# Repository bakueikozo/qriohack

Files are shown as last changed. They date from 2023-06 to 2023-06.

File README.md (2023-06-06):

# qriohack
Qrio Lock 初代(Q-SL1)をハックするための知見と  
内蔵マイコンを書き換えるためのファームを生成するためのソースコードです

# 現状の実装
設定に追加のシリアルポートが必要
鍵を施錠位置に合わせて取り付けて'P'コマンドで初期位置入力  
続けて鍵を開錠位置に合わせて取り付けて'P'コマンドで第二位置入力すると記憶される  
開錠したいときはシリアルから'U' 、施錠は'L'を送る  
もしくは、BLE送信できる奴から特定のところに'U'か'L'を書き込むと動く  

これをアプリから送るようにUIを作ると今までのQrioのように作れます。
が、まだ作ってませんし、私が作るとは言ってません。
# どうやる
Windowsの場合
WICED-SDKをダウンロードしてきて、Apps以下にこのリポジトリ内のApps/obaqフォルダをコピーします
コマンドプロンプトから
> make obaq-BCM920737TAG_Q32

でビルドできるか確認

OKなら
> make obaq-BCM920737TAG_Q32 download UART=COMxx

で書き込み

WICED-SDKは
https://community.infineon.com/t5/Public-Archive/WICED-Smart-SDK-2-2-3-7z-Archive/td-p/247688

ここにある奴で確認済み
そのほかのバージョンやIDEにインポートするなら各自

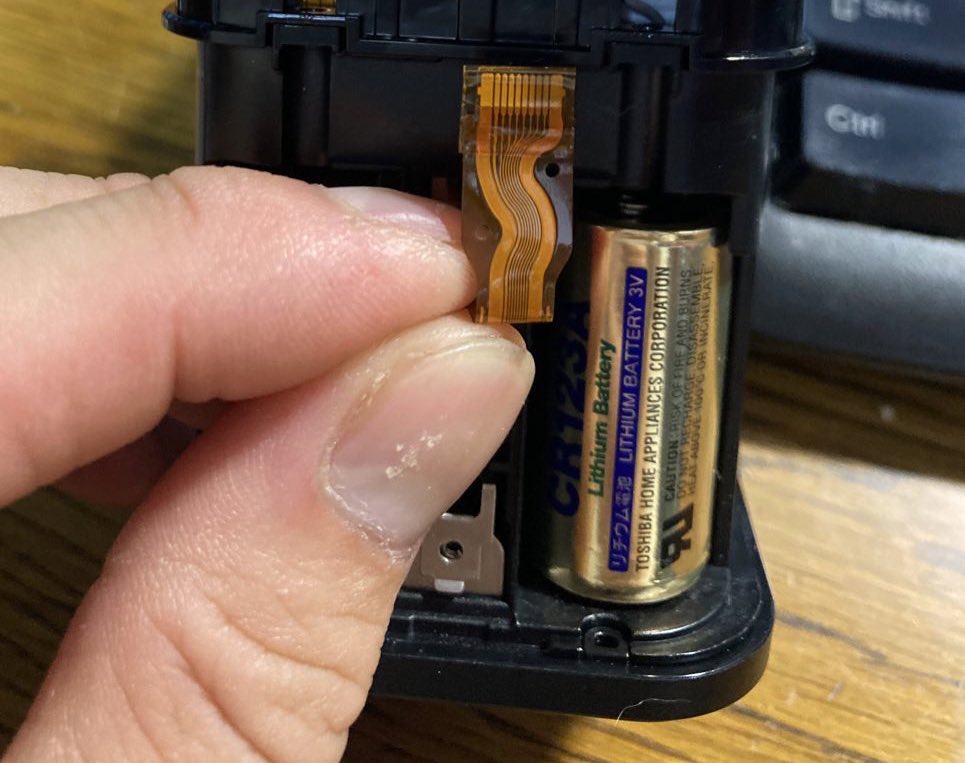
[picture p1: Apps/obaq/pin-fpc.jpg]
書き込みコネクタ


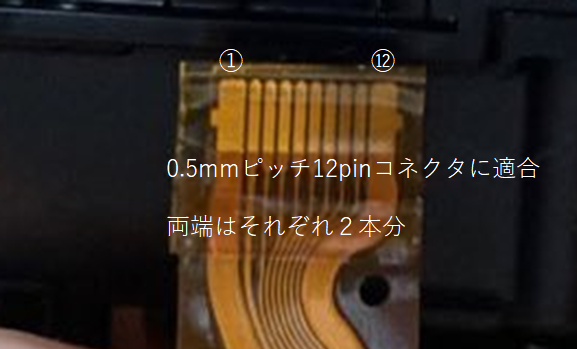
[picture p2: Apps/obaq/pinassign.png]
ピンアサイン ピン番号の見方


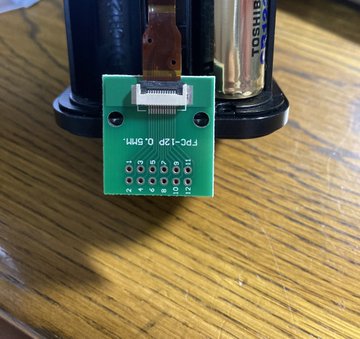
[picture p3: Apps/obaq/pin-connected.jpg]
変換基板に取り付けた場合


# ピンアサイン
下面接続のFPC基板に取り付けた場合、この説明の番号と一致します  
使ったやつはこれ　 https://amzn.to/43Kj0qI  
|  No. |  Function  |
| ---- | ---- |
|  1,2  |  6V  |
|  3  |  3.3V  |
| 4 | RESET(NC:基板上ジャンパ)  
| 5 |SCL(NC:基板上ジャンパ)  |
| 6 | SDA(NC:基板上ジャンパ) |
| 7 |peripheral UART TXD in  |
| 8 |peripheral UART RXD out  |
| 9 |Programming RXD  |
| 10 |Programing TXD  |
| 11,12 |GND  |

1,2および3　は基板上の電源パターン直結のため、電池が入っているときの挙動に注意  
4,5,6は基板まで届いているが、基板上でジャンパがNCになっているのでそのままでは使用不可   
9,10と3,11,12の接続で書き込み可能。電源投入時に9をHighにしておくとProgrammingモードに入る   

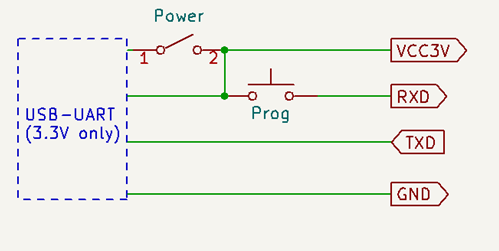
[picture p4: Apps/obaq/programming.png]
書き込み回路


追加のシリアルポートが欲しい場合は7,8を使う  

※参考※  
https://community.infineon.com/t5/Resource-Library/Programming-the-TAG2-TAG3-Board-using-command-line-tools/ta-p/246905  
書き込み中に電源を落としてしまった場合正常に起動しなくなる。その場合downloadではなくrecoveryモードに入る必要がある。  
電源投入orRESETの際にeepromのSDAをVCCに吊るとソフトが読み込めない→リカバリモードになる  
ここでrecoveryで書き込む

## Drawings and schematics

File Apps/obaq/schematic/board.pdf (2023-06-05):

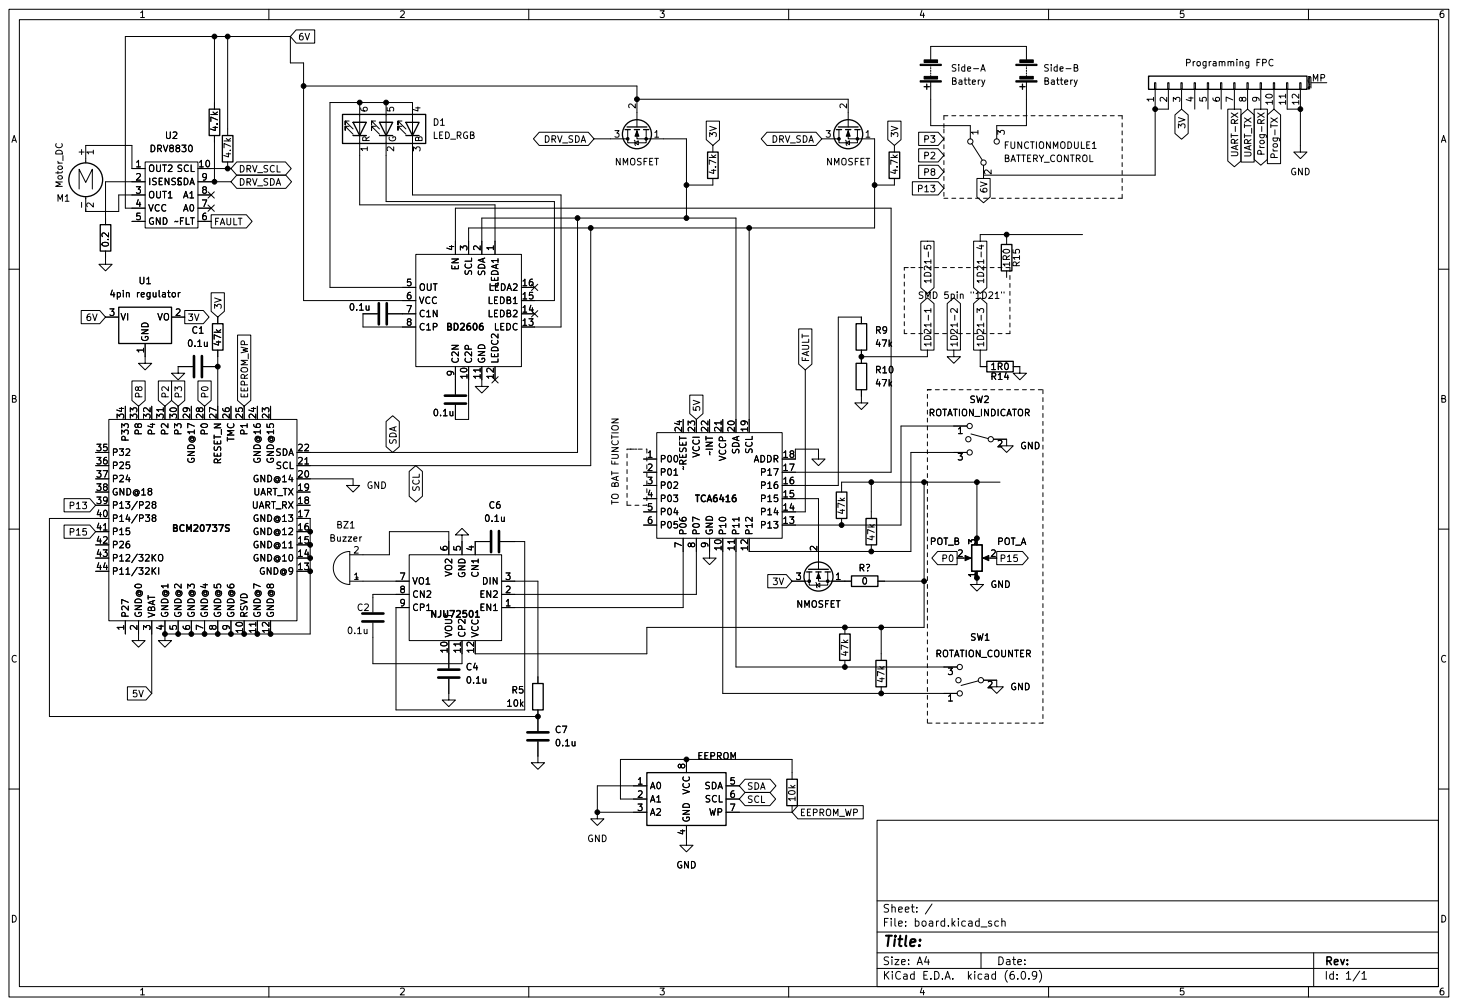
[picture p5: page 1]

2 GND@14 20 SCL 21 SDA 22 GND@15 23 GND@16 24 P1 25 TMC 26 RESET_N 27 P0 28 GND@17 29 VBAT

1 RSVD 10 GND@7 11 GND@8 12 GND@9 13 GND@10 14 GND@11 15 GND@12 16 GND@13 17 UART_RX 18 UART_TX 19 GND@0

4 SDA 5 SCL 6 WP 7 VCC

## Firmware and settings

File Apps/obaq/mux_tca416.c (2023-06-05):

// TCA6416A module
// Copyright 2019 Håkon Nessjøen
// https://github.com/haakonnessjoen/TCA6416A/


#include "bleprofile.h"
#include "bleapp.h"
#include "gpiodriver.h"
#include "string.h"
#include "stdio.h"
#include "platform.h"
#include "bleappconfig.h"
#include "cfa.h"


#include "mux_tca416.h"

void tca_begin(UINT8 address){
    ble_trace0("tca_begin\n");
	tca_i2caddr = 0x20 | address;
	tca_i2caddr =tca_i2caddr<<1 ;
	tca_i2cwidth = 2;

	tca_port_read();
	tca_mode_read();
    ble_trace0("tca_end\n");
}
void tca_pin_mode(UINT8 pinNum, int mode){
	UINT16 mask = 1 << pinNum;
    ble_trace0("tca_pin_mode\n");

	if (mode == TCA_PINMODE_INPUT) {
		tca_pinModes |= mask;
	} else {
		tca_pinModes &= ~mask;
	}

	tca_mode_write(tca_pinModes);
}


void tca_pin_write(UINT8 pinNum, UINT8 level){
	UINT16 mask = 1 << pinNum;
    ble_trace0("tca_pin_write\n");

	if (level == TCA_OUTPUT_HIGH) {
		tca_pinState |= mask;
	} else {
		tca_pinState &= ~mask;
	}

	tca_port_write(tca_pinState);
}
INT16  tca_pin_read(UINT8 pinNum){
	UINT16 mask = 1 << pinNum;
    ble_trace0("tca_pin_read\n");

	tca_port_read();

	if ((tca_pinState & mask) == mask) {
		return 1;
	} else {
		return 0;
	}
}
void tca_port_write(UINT16 i2cportval){

    CFA_BSC_STATUS read_status;
    UINT8 return_value = 0;

    UINT8 reg_bytes_to_write[3];
    reg_bytes_to_write[0] = TCAREG_OUTPUT0;
    reg_bytes_to_write[1] = i2cportval & 0xFF;
    reg_bytes_to_write[2] = (i2cportval >> 8) & 0xFF;
    ble_trace0("tca_port_write\n");

    // Invoke the lower level driver. Non-combo transaction, so set offset parameters to NULL/0.
    read_status = cfa_bsc_OpExtended(reg_bytes_to_write, sizeof(reg_bytes_to_write), NULL, 0, tca_i2caddr,
                                                I2C_SLAVE_OPERATION_WRITE);

    switch(read_status)
    {
        case CFA_BSC_STATUS_INCOMPLETE:
            // Transaction did not go through. ERROR. Handle this case.
            break;
        case CFA_BSC_STATUS_SUCCESS:
		    ble_trace0("i2c_write success\n");
            return_value = 1;
            break;
        case CFA_BSC_STATUS_NO_ACK:
            // No slave device with this address exists on the I2C bus. ERROR. Handle this.
        default:
            break;
    }

	tca_pinState = i2cportval;
}
UINT16 tca_port_read(){
// (UINT8 slave_address,UINT8 register_address, INT16* data// 

    CFA_BSC_STATUS read_status;
    UINT8 return_value = 0;

    UINT8 reg_read_bytes_to_write[1];
    UINT8 reg_bytes_to_read[2];
	INT16 data;
    ble_trace0("tca_port_read\n");
    
    reg_read_bytes_to_write[0] = TCAREG_INPUT0;

    // Do a combo write then read operation
    read_status = cfa_bsc_OpExtended(reg_bytes_to_read, sizeof(reg_bytes_to_read), reg_read_bytes_to_write,
                                                        sizeof(reg_read_bytes_to_write), tca_i2caddr,
                                                        I2C_SLAVE_OPERATION_READ);
    switch(read_status)
    {
        case CFA_BSC_STATUS_INCOMPLETE:
            // Transaction did not go through. ERROR. Handle this case.
            break;
        case CFA_BSC_STATUS_SUCCESS:
            // The read was successful.
            data = (INT16)(reg_bytes_to_read[0] | reg_bytes_to_read[1] << 8);
			tca_pinState = (tca_pinState & ~tca_pinModes) | (data & tca_pinModes);

		    ble_trace0("i2c_read success\n");

            return tca_pinState;
        case CFA_BSC_STATUS_NO_ACK:
            // No slave device with this address exists on the I2C bus. ERROR. Handle this.
        default:
            break;
    }

    return -1;

}
void tca_mode_write(UINT16 modes){
    CFA_BSC_STATUS read_status;
    UINT8 return_value = 0;

    UINT8 reg_bytes_to_write[3];
    ble_trace0("tca_mode_write\n");

    reg_bytes_to_write[0] = TCAREG_CONFIG0;
    reg_bytes_to_write[1] = modes & 0xFF;
    reg_bytes_to_write[2] = (modes >> 8) & 0xFF;

    // Invoke the lower level driver. Non-combo transaction, so set offset parameters to NULL/0.
    read_status = cfa_bsc_OpExtended(reg_bytes_to_write, sizeof(reg_bytes_to_write), NULL, 0, tca_i2caddr,
                                                I2C_SLAVE_OPERATION_WRITE);

    switch(read_status)
    {
        case CFA_BSC_STATUS_INCOMPLETE:
            // Transaction did not go through. ERROR. Handle this case.
		    ble_trace0("i2c_write INCOMP\n");
            break;
        case CFA_BSC_STATUS_SUCCESS:
            // The read was successful.
		    ble_trace0("i2c_write success\n");
            return_value = 1;
            break;
        case CFA_BSC_STATUS_NO_ACK:
		    ble_trace0("i2c_write NO_ACK\n");
            // No slave device with this address exists on the I2C bus. ERROR. Handle this.
        default:
		    ble_trace0("default\n");
            break;
    }


	tca_pinModes = modes;
}
UINT16 tca_mode_read(){
    CFA_BSC_STATUS read_status;
    UINT8 return_value = 0;

    UINT8 reg_read_bytes_to_write[1];
    UINT8 reg_bytes_to_read[2];
    ble_trace0("tca_mode_read\n");

    reg_read_bytes_to_write[0] = TCAREG_CONFIG0;

    // Do a combo write then read operation
    read_status = cfa_bsc_OpExtended(reg_bytes_to_read, sizeof(reg_bytes_to_read), reg_read_bytes_to_write,
                                                        sizeof(reg_read_bytes_to_write), tca_i2caddr,
                                                        I2C_SLAVE_OPERATION_READ);
    switch(read_status)
    {
        case CFA_BSC_STATUS_INCOMPLETE:
            // Transaction did not go through. ERROR. Handle this case.
            break;
        case CFA_BSC_STATUS_SUCCESS:
            // The read was successful.
            {
            INT16 data = (INT16)(reg_bytes_to_read[0] | reg_bytes_to_read[1] << 8);
            return_value = 1;

			/*
			tca_pinModes = TW.read();
			tca_pinModes |= TW.read() << 8;*/

			tca_pinModes = data;
		    ble_trace0("i2c_read success\n");
			}		
            break;
        case CFA_BSC_STATUS_NO_ACK:
            // No slave device with this address exists on the I2C bus. ERROR. Handle this.
        default:
            break;
    }


	return tca_pinModes;
}
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

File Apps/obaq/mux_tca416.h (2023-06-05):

// TCA6416A module
// Copyright 2019 Håkon Nessjøen
// https://github.com/haakonnessjoen/TCA6416A/

#define TCA_PINMODE_INPUT 0
#define TCA_PINMODE_OUTPUT 1
#define TCA_OUTPUT_HIGH 1
#define TCA_OUTPUT_LOW 0

// Read operation to the lower level driver is 0.
#define I2C_SLAVE_OPERATION_READ                    (0)

// Write operation to the lower level driver is 1.
#define I2C_SLAVE_OPERATION_WRITE                   (1)


#define TCAREG_INPUT0 0x00
#define TCAREG_INPUT1 0x01
#define TCAREG_OUTPUT0 0x02
#define TCAREG_OUTPUT1 0x03
#define TCAREG_POLARITY0 0x04
#define TCAREG_POLARITY1 0x05
#define TCAREG_CONFIG0 0x06
#define TCAREG_CONFIG1 0x07


UINT8 tca_i2caddr;
UINT8 tca_i2cwidth;
UINT16 tca_pinState;
UINT16 tca_pinModes;
void tca_pin_mode(UINT8 pinNum, int mode);
void tca_pin_write(UINT8 pinNum, UINT8 level);
INT16 tca_pin_read(UINT8 pinNum);
void tca_port_write(UINT16 i2cportval);
UINT16 tca_port_read();
void tca_mode_write(UINT16 i2cportval);
UINT16 tca_mode_read();

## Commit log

2023-06-05 kicad files
    [board.kicad_pcb, board.kicad_sch]
2023-06-06 add pin
